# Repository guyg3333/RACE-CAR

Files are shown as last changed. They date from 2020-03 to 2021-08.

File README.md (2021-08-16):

# RACE-CAR

This repository contain my Academic engineering final project, which try to suggest a method of organizing information traffic in autonomous vehicles,

The problem I wanted to solve is how to expand the current communication method to support Advanced Drive assist application.

The proposed solution is to build a network built from a combination of CAN bus and Ethernet interfaces, were Ethernet used as backbone.

To bridge between the two interfaces I suggested to add dedicated module That I call  "Gateway Node",

The Gateway Node aim to manage the car data traffic and with him create a hierarchical Democratic multi master network were every node can exchange data.

### Network components
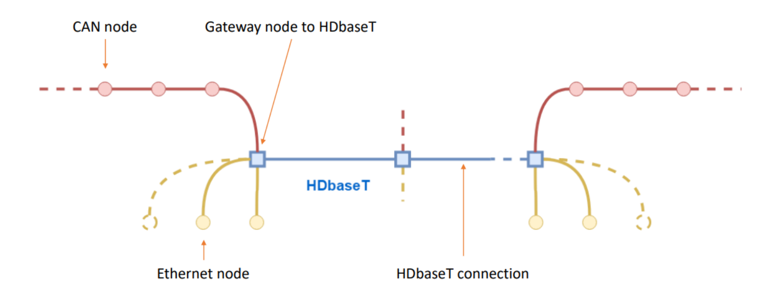
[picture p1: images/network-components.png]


### Network concept

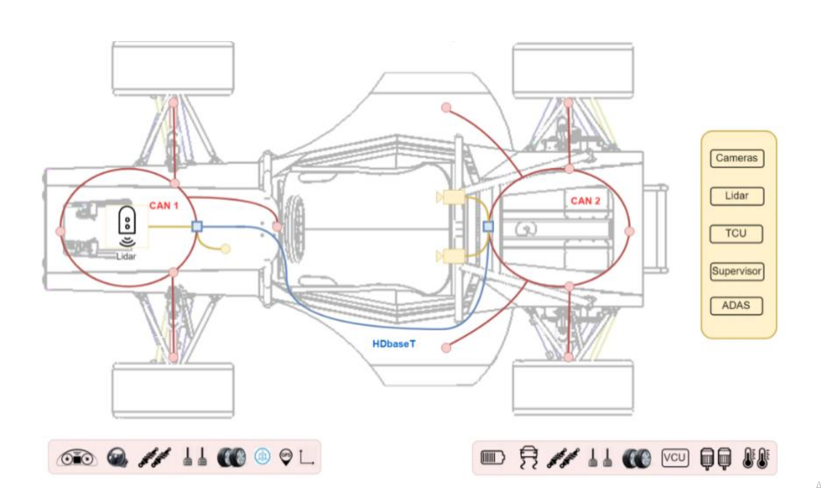
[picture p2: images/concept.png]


### Gateway Node 3D Model

I design and implement the network module "Gateway Node"

To meet the requirements of critical information passing through a vehicle, the Ethernet interface supports the AVB protocol to Ensure real time policy. [Link to PCB repository ](https://github.com/guyg3333/AVB_Ethernet_switch_with_CAN_bus)

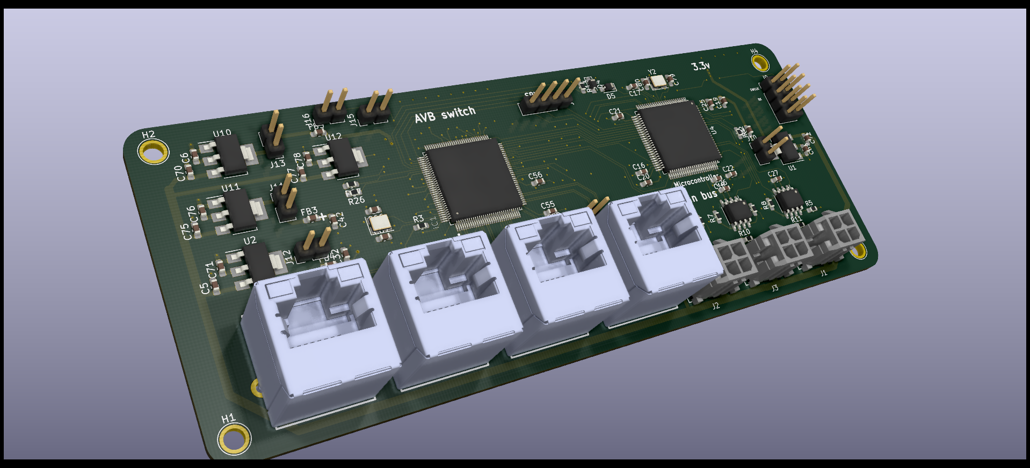
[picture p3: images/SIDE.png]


### CAN Node 3D Model

### Ben Gurion Racing

The component was assimilated in Ben-Gurion University FSAE electric car in 2019

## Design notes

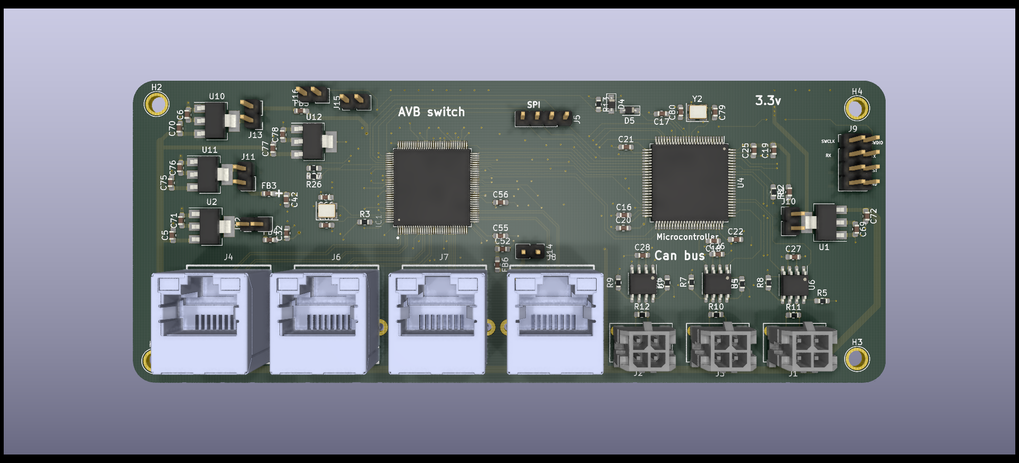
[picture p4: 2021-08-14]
images/TOP.png

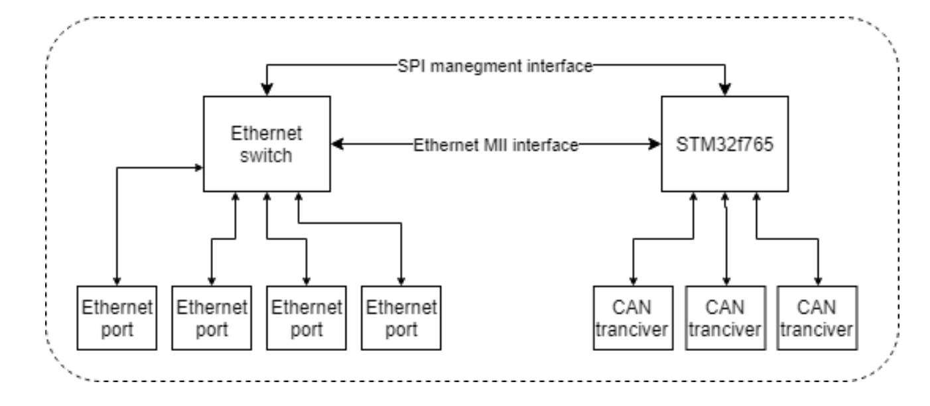
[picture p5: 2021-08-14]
images/block_diagram.png

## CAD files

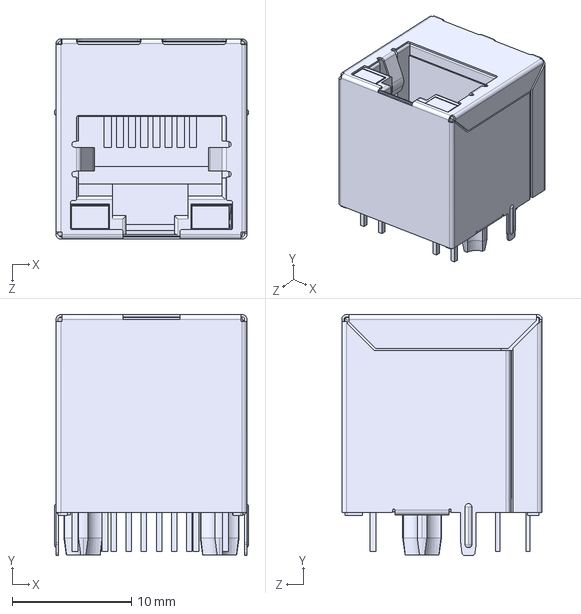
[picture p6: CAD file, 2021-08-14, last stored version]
AVB Ethernet switch with Can bus/3d/JD2_JXD2-0010N.STEP
16.3 x 20.2 x 16.8 mm

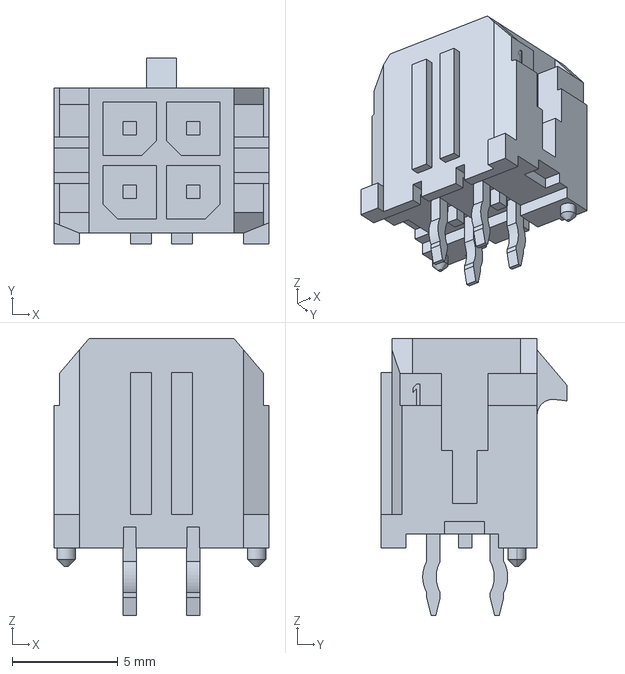
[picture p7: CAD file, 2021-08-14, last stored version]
AVB_Ethernet_switch_with_CAN_bus/3d/430450413.STEP
10.2 x 8.77 x 13.1 mm

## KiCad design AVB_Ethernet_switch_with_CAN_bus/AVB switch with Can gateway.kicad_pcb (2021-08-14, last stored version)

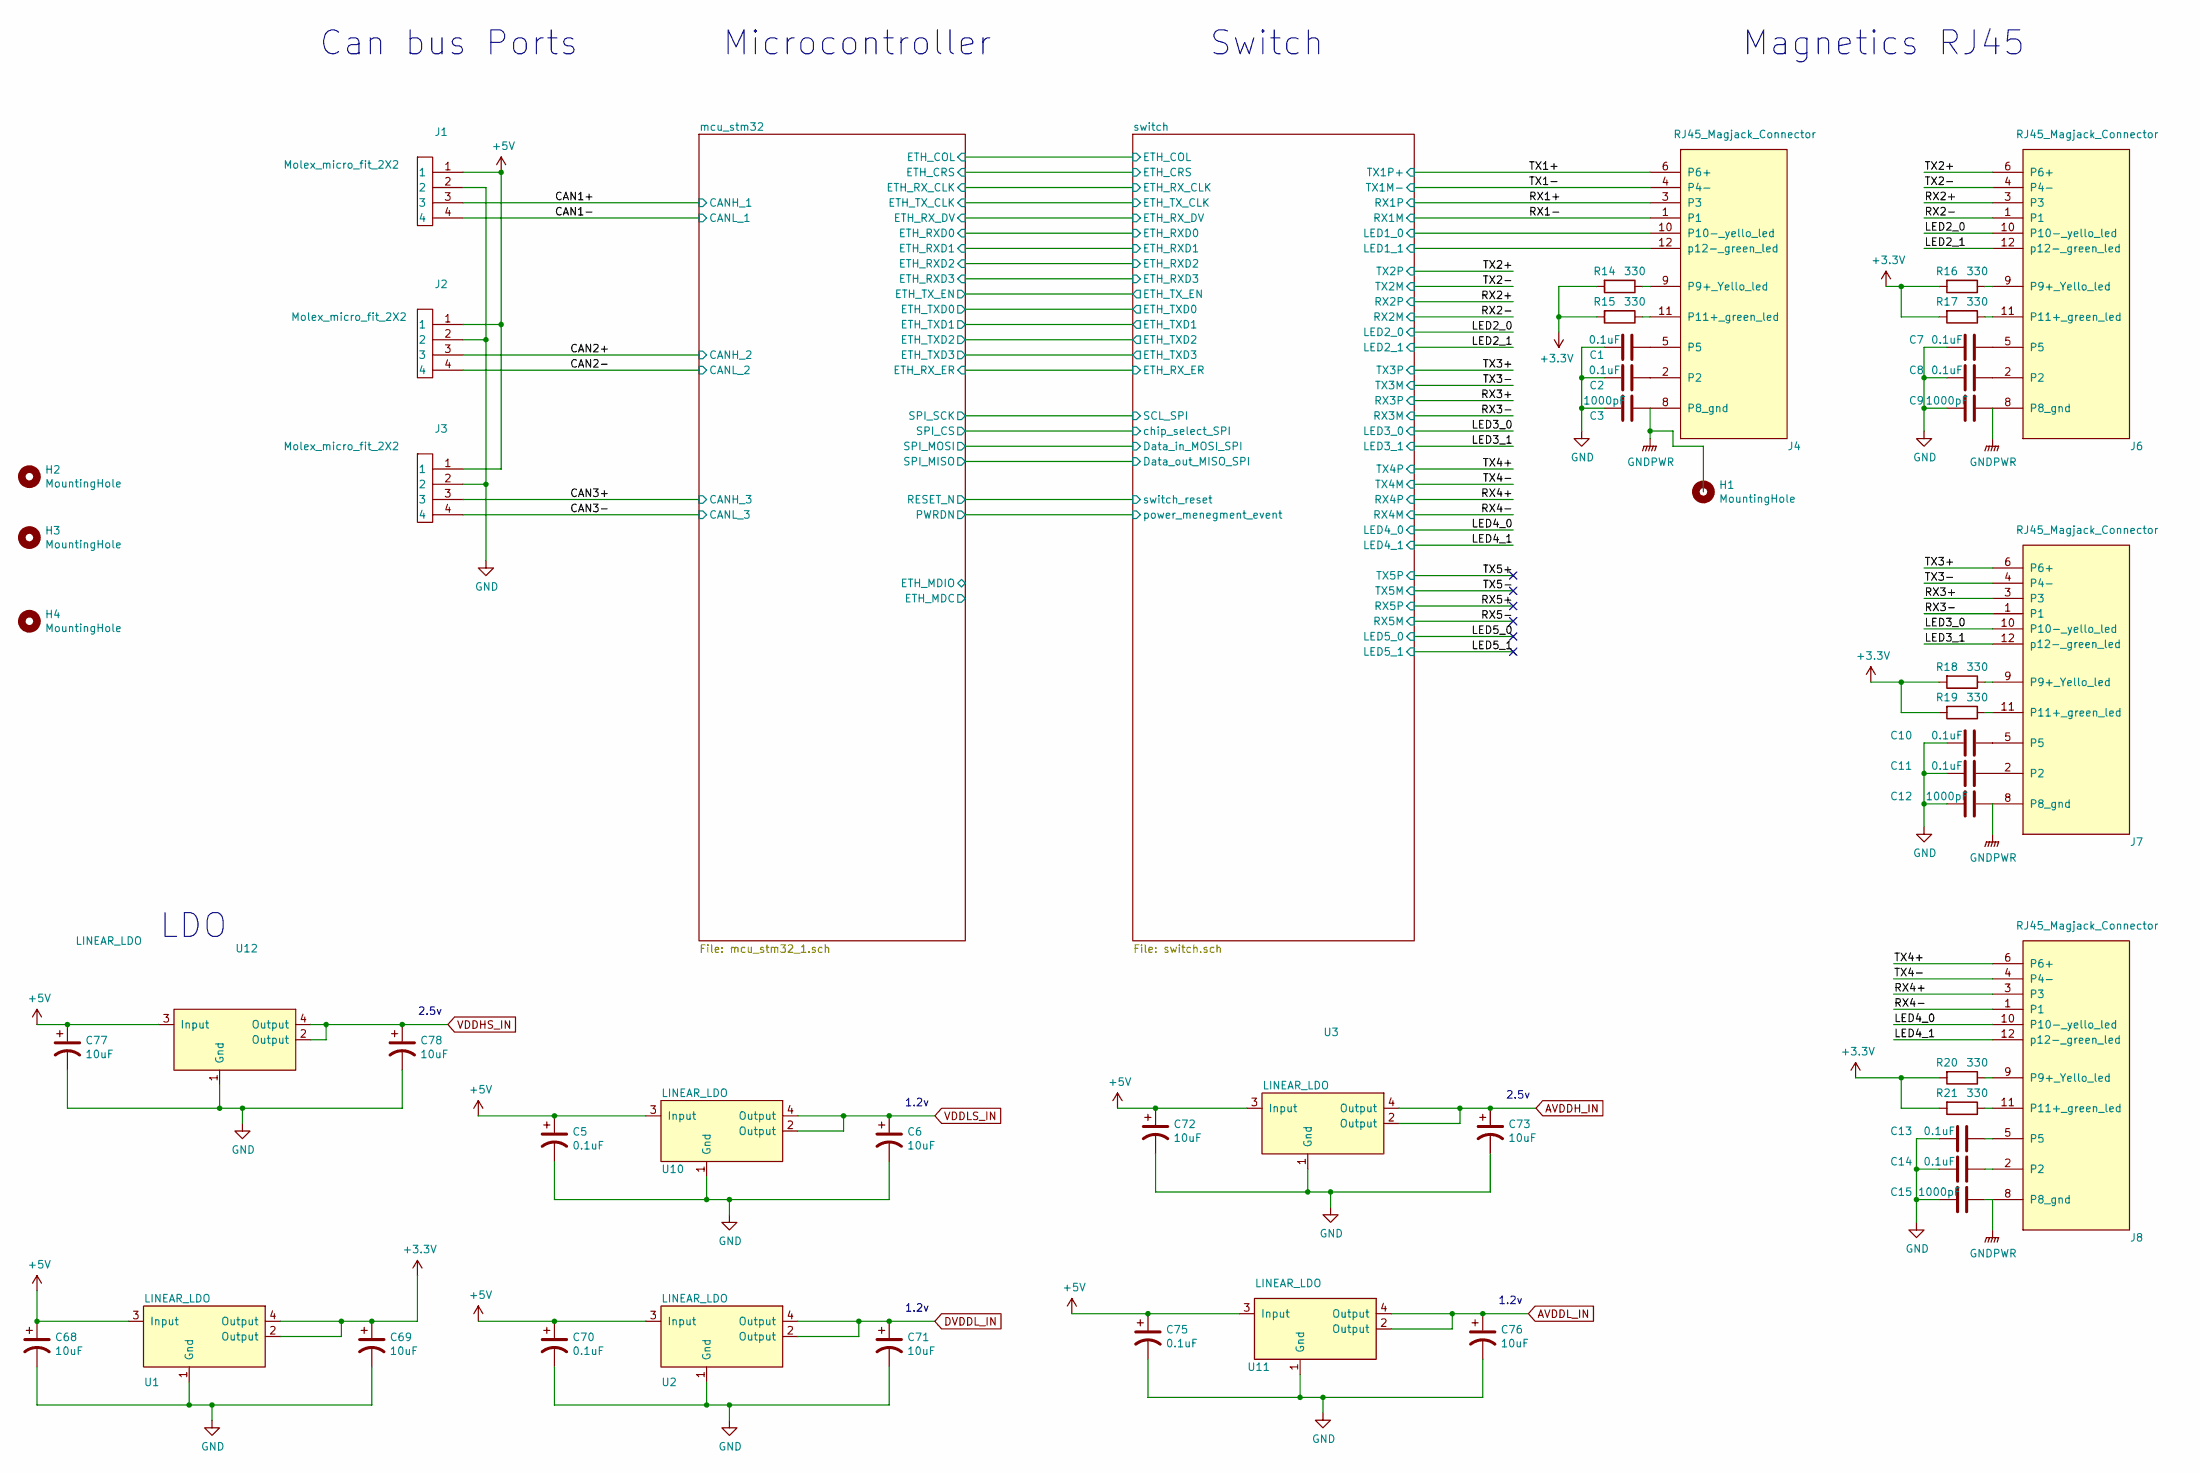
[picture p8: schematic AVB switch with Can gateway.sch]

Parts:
C1, C2, C7, C8, C10, C11, C13, C14: 0.1uF; C_0603_1608Metric_Pad1.05x0.95mm_HandSolder; Manufacturer_Part_Number C0603C104J4RACTU‎‏
C3, C9, C12, C15: 1000pF; C_0603_1608Metric_Pad1.05x0.95mm_HandSolder; Manufacturer_Part_Number C0603V102KDRAC7867‎‏
C5, C70, C75: 0.1uF; C_0603_1608Metric_Pad1.05x0.95mm_HandSolder; Manufacturer_Part_Number CC1206KRX7R9BB104‎‏
C6, C68, C69, C71, C72, C73, C76, C77, C78: 10uF; C_0603_1608Metric_Pad1.05x0.95mm_HandSolder; Manufacturer_Part_Number T520A106M010ATE080‎‏
H1, H2, H3, H4: MountingHole; 1pin
J1, J2, J3: Molex_micro_fit_2X2; Manufacturer_Part_Number ‏‎CONN HEADER VERT 4POS 3MM‎‏
J4, J6, J7, J8: RJ45_Magjack_Connector; RJ45_MAGJACK_1PORT_100_BASE-T‎‏; Manufacturer_Part_Number ‏‎JD2-0010NL‎‏
R14, R15, R16, R17, R18, R19, R20, R21: 330; R_0603_1608Metric_Pad1.05x0.95mm_HandSolder; Manufacturer_Part_Number ‏‎CR0603-JW-331ELF‎‏
U1: LINEAR_LDO; SOT-223; Manufacturer_Part_Number NCP1117ST33T3G‎‏
U2, U10, U11: LINEAR_LDO; SOT-223; Manufacturer_Part_Number LD1117AS12TR‎‏
U3, U12: LINEAR_LDO; SOT-223; Manufacturer_Part_Number ‏‎NCV1117ST25T3G‎‏

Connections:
+3V3: C69.1, R14.2, R15.2, R16.2, R17.2, R18.2, R19.2, R20.2, R21.2, U1.2 (Output), U1.4 (Output); also elsewhere on the board
+5V: C5.1, C68.1, C70.1, C72.1, C75.1, C77.1, J1.1, J2.1, J3.1, U1.3 (Input), U2.3 (Input), U3.3 (Input), U10.3 (Input), U11.3 (Input), U12.3 (Input)
/CAN1+: J1.3; also elsewhere on the board
/CAN1-: J1.4; also elsewhere on the board
/CAN2+: J2.3; also elsewhere on the board
/CAN2-: J2.4; also elsewhere on the board
/CAN3+: J3.3; also elsewhere on the board
/CAN3-: J3.4; also elsewhere on the board
/LED2_0: J6.10 (P10-_yello_led); also elsewhere on the board
/LED2_1: J6.12 (p12-_green_led); also elsewhere on the board
/LED3_0: J7.10 (P10-_yello_led); also elsewhere on the board
/LED3_1: J7.12 (p12-_green_led); also elsewhere on the board
/LED4_0: J8.10 (P10-_yello_led); also elsewhere on the board
/LED4_1: J8.12 (p12-_green_led); also elsewhere on the board
/RX1+: J4.3; also elsewhere on the board
/RX1-: J4.1; also elsewhere on the board
/RX2+: J6.3; also elsewhere on the board
/RX2-: J6.1; also elsewhere on the board
/RX3+: J7.3; also elsewhere on the board
/RX3-: J7.1; also elsewhere on the board
/RX4+: J8.3; also elsewhere on the board
/RX4-: J8.1; also elsewhere on the board
/TX1+: J4.6 (P6+); also elsewhere on the board
/TX1-: J4.4 (P4-); also elsewhere on the board
/TX2+: J6.6 (P6+); also elsewhere on the board
/TX2-: J6.4 (P4-); also elsewhere on the board
/TX3+: J7.6 (P6+); also elsewhere on the board
/TX3-: J7.4 (P4-); also elsewhere on the board
/TX4+: J8.6 (P6+); also elsewhere on the board
/TX4-: J8.4 (P4-); also elsewhere on the board
/switch/LED1_0: J4.10 (P10-_yello_led); also elsewhere on the board
/switch/LED1_1: J4.12 (p12-_green_led); also elsewhere on the board
AVDDH_IN: C73.1, U3.2 (Output), U3.4 (Output); also elsewhere on the board
AVDDL_IN: C76.1, U11.2 (Output), U11.4 (Output); also elsewhere on the board
DVDDL_IN: C71.1, U2.2 (Output), U2.4 (Output); also elsewhere on the board
GND: C1.2, C2.2, C3.2, C5.2, C6.2, C7.2, C8.2, C9.2, C10.2, C11.2, C12.2, C13.2, C14.2, C15.2, C68.2, C69.2, C70.2, C71.2, C72.2, C73.2, C75.2, C76.2, C77.2, C78.2, J1.2, J2.2, J3.2, U1.1 (Gnd), U2.1 (Gnd), U3.1 (Gnd), U10.1 (Gnd), U11.1 (Gnd), U12.1 (Gnd); also elsewhere on the board
GNDPWR: C3.1, C9.1, C12.1, C15.1, J4.8 (P8_gnd), J6.8 (P8_gnd), J7.8 (P8_gnd), J8.8 (P8_gnd)
unnamed: C1.1, J4.5
unnamed: C2.1, J4.2
unnamed: C7.1, J6.5
unnamed: C8.1, J6.2
unnamed: C10.1, J7.5
unnamed: C11.1, J7.2
unnamed: C13.1, J8.5
unnamed: C14.1, J8.2
unnamed: J4.9 (P9+_Yello_led), R14.1
unnamed: J4.11 (P11+_green_led), R15.1
unnamed: J6.9 (P9+_Yello_led), R16.1
unnamed: J6.11 (P11+_green_led), R17.1
unnamed: J7.9 (P9+_Yello_led), R18.1
unnamed: J7.11 (P11+_green_led), R19.1
unnamed: J8.9 (P9+_Yello_led), R20.1
unnamed: J8.11 (P11+_green_led), R21.1
VDDHS_IN: C78.1, U12.2 (Output), U12.4 (Output); also elsewhere on the board
VDDLS_IN: C6.1, U10.2 (Output), U10.4 (Output); also elsewhere on the board

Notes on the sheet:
Switch
Microcontroller
Can bus Ports
Magnetics RJ45
LDO
2.5v
1.2v

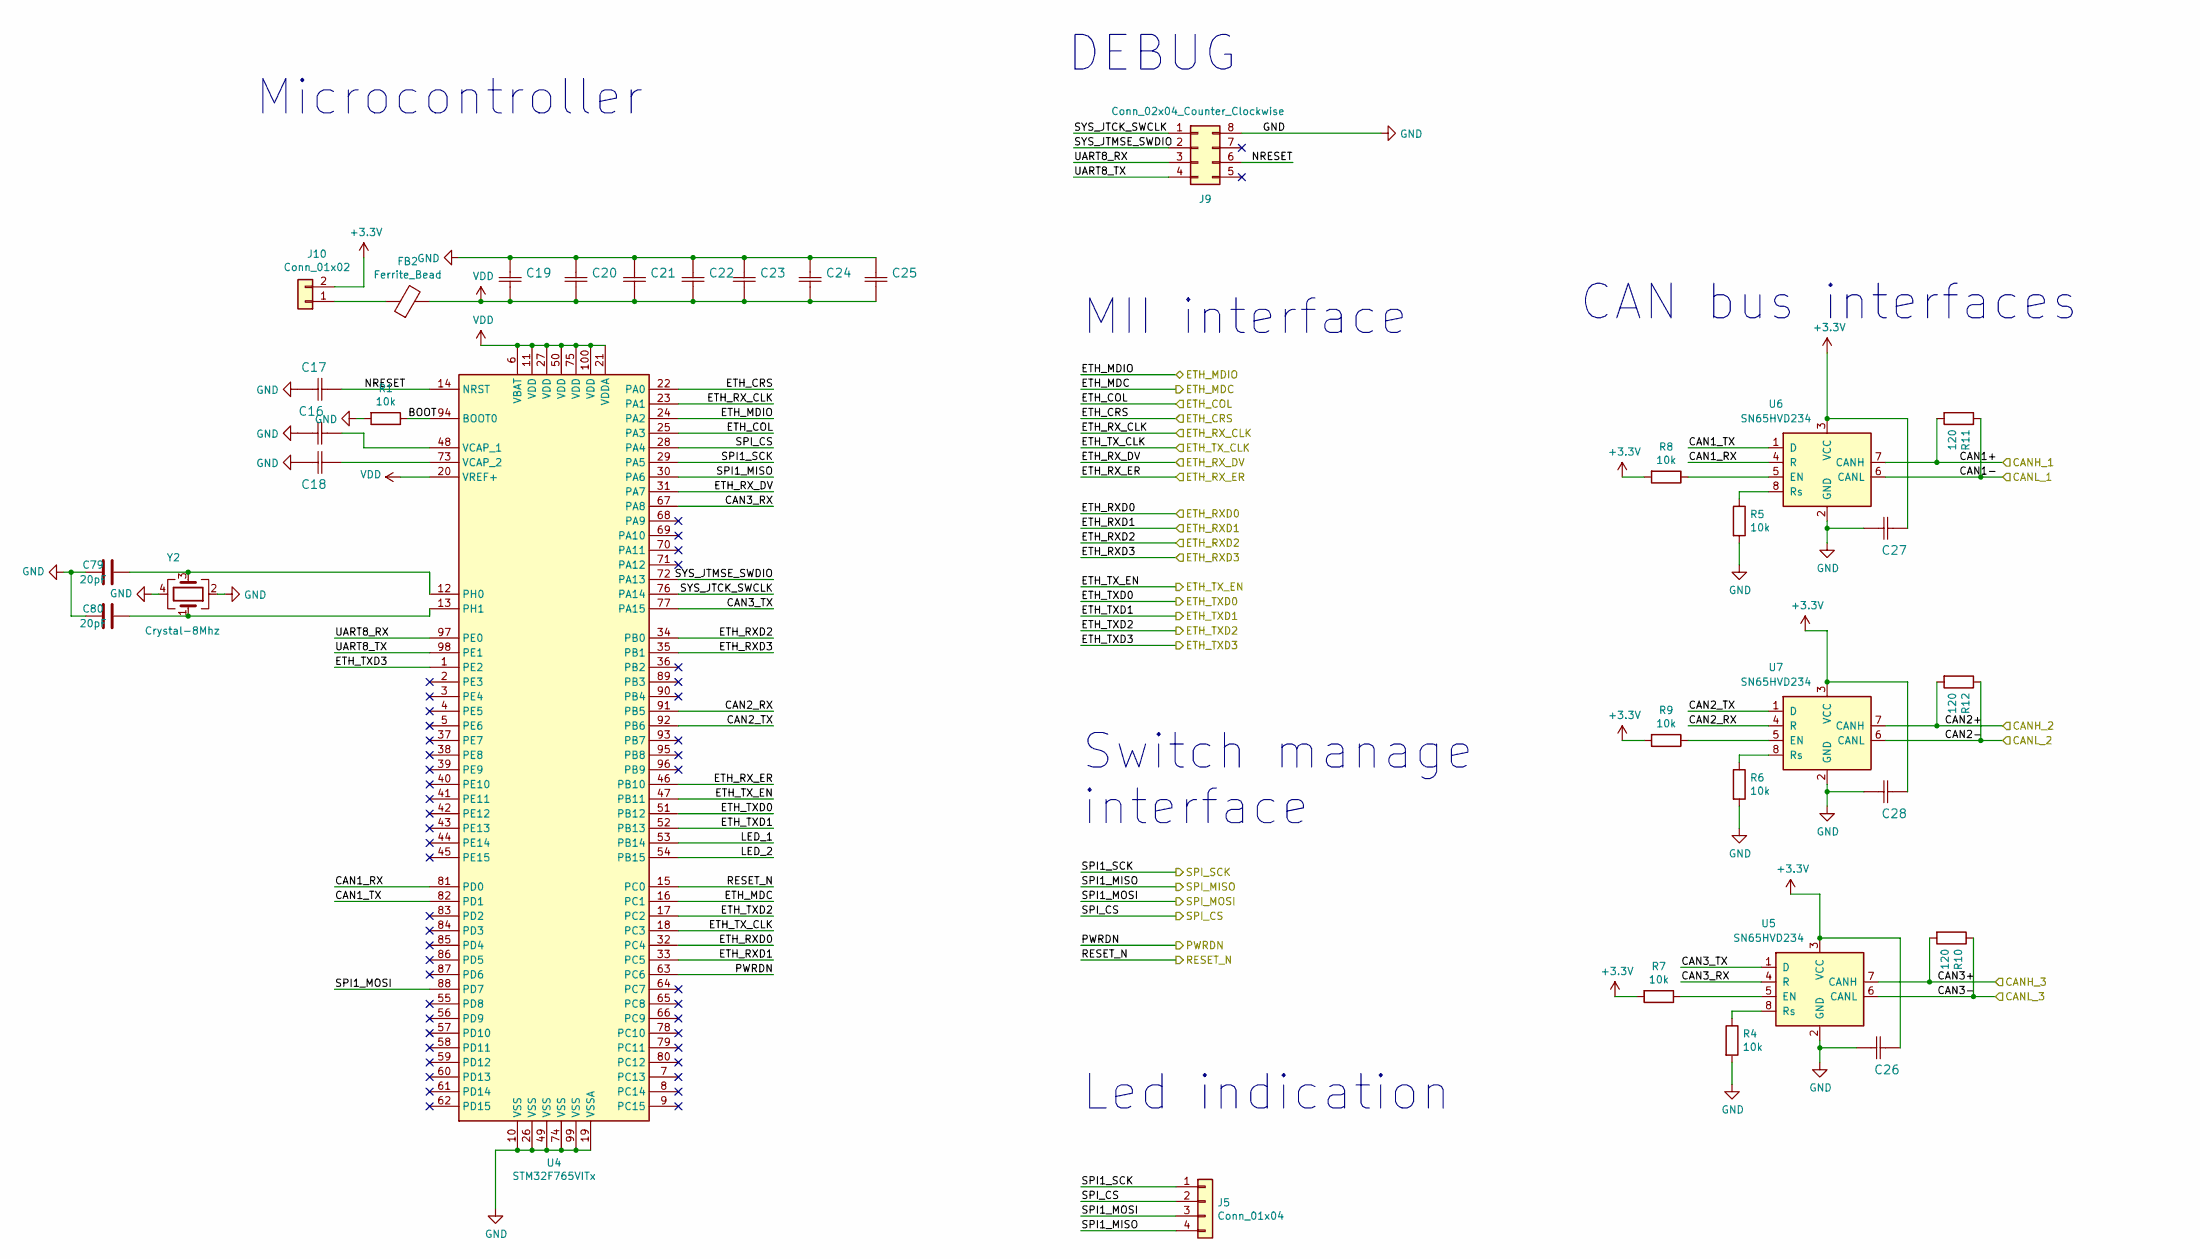
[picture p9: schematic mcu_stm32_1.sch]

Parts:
C16, C18, C26, C27, C28: 2.2uF; C_0603_1608Metric_Pad1.05x0.95mm_HandSolder; Manufacturer_Part_Number CL10A225KP8NNNC‎‏
C17, C20, C21, C22, C23, C24, C25: 0.1uF; C_0603_1608Metric_Pad1.05x0.95mm_HandSolder; Manufacturer_Part_Number C0603C104J4RACTU‎‏
C19: 4.7uF; C_0603_1608Metric_Pad1.05x0.95mm_HandSolder; Manufacturer_Part_Number CL10B475KQ8NQNC‎‏
C79, C80: 20pF; C_0603_1608Metric_Pad1.05x0.95mm_HandSolder; Manufacturer_Part_Number CL10C360JB8NNNC‎‏
FB2: Ferrite_Bead; C_0603_1608Metric_Pad1.05x0.95mm_HandSolder
J5: Conn_01x04; PinHeader_1x04_P2.54mm_Vertical
J9: Conn_02x04_Counter_Clockwise; PinHeader_2x04_P2.54mm_Vertical
J10: Conn_01x02; PinHeader_1x02_P2.54mm_Vertical
R1: 10k; R_0603_1608Metric_Pad1.05x0.95mm_HandSolder
R4, R5, R6, R7, R8, R9: 10k; R_0603_1608Metric_Pad1.05x0.95mm_HandSolder; Manufacturer_Part_Number RNCP0603FTD10K0‎‏
R10, R11, R12: 120; R_0603_1608Metric_Pad1.05x0.95mm_HandSolder; Manufacturer_Part_Number ‏‎CRGCQ0603F120R‎‏
U4: STM32F765VITx; LQFP-100_14x14mm_P0.5mm; Manufacturer_Part_Number ‏‎STM32F765VIT6‎‏
U5, U6, U7: SN65HVD234; SOIC-8_3.9x4.9mm_P1.27mm; Manufacturer_Part_Number SN65HVD234DR‎‏
Y2: Crystal-8Mhz; Crystal_SMD_3225-4Pin_3.2x2.5mm; Manufacturer_Part_Number ‏‎ECS-80-10-30B-CWN-TR‎‏

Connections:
+3V3: C26.1, C27.1, C28.1, J10.2, R7.2, R8.2, R9.2, U5.3 (VCC), U6.3 (VCC), U7.3 (VCC); also elsewhere on the board
/CAN1+: R11.2, U6.7 (CANH); also elsewhere on the board
/CAN1-: R11.1, U6.6 (CANL); also elsewhere on the board
/CAN2+: R12.2, U7.7 (CANH); also elsewhere on the board
/CAN2-: R12.1, U7.6 (CANL); also elsewhere on the board
/CAN3+: R10.2, U5.7 (CANH); also elsewhere on the board
/CAN3-: R10.1, U5.6 (CANL); also elsewhere on the board
/mcu_stm32/BOOT: R1.1, U4.94 (BOOT0)
/mcu_stm32/CAN1_RX: U4.81 (PD0), U6.4 (R)
/mcu_stm32/CAN1_TX: U4.82 (PD1), U6.1 (D)
/mcu_stm32/CAN2_RX: U4.91 (PB5), U7.4 (R)
/mcu_stm32/CAN2_TX: U4.92 (PB6), U7.1 (D)
/mcu_stm32/CAN3_RX: U4.67 (PA8), U5.4 (R)
/mcu_stm32/CAN3_TX: U4.77 (PA15), U5.1 (D)
/mcu_stm32/ETH_COL: U4.25 (PA3); also elsewhere on the board
/mcu_stm32/ETH_CRS: U4.22 (PA0); also elsewhere on the board
/mcu_stm32/ETH_MDC: U4.16 (PC1)
/mcu_stm32/ETH_MDIO: U4.24 (PA2)
/mcu_stm32/ETH_RXD0: U4.32 (PC4); also elsewhere on the board
/mcu_stm32/ETH_RXD1: U4.33 (PC5); also elsewhere on the board
/mcu_stm32/ETH_RXD2: U4.34 (PB0); also elsewhere on the board
/mcu_stm32/ETH_RXD3: U4.35 (PB1); also elsewhere on the board
/mcu_stm32/ETH_RX_CLK: U4.23 (PA1); also elsewhere on the board
/mcu_stm32/ETH_RX_DV: U4.31 (PA7); also elsewhere on the board
/mcu_stm32/ETH_RX_ER: U4.46 (PB10); also elsewhere on the board
/mcu_stm32/ETH_TXD0: U4.51 (PB12); also elsewhere on the board
/mcu_stm32/ETH_TXD1: U4.52 (PB13); also elsewhere on the board
/mcu_stm32/ETH_TXD2: U4.17 (PC2); also elsewhere on the board
/mcu_stm32/ETH_TXD3: U4.1 (PE2); also elsewhere on the board
/mcu_stm32/ETH_TX_CLK: U4.18 (PC3); also elsewhere on the board
/mcu_stm32/ETH_TX_EN: U4.47 (PB11); also elsewhere on the board
/mcu_stm32/LED_1: U4.53 (PB14)
/mcu_stm32/LED_2: U4.54 (PB15)
/mcu_stm32/NRESET: C17.1, J9.6, U4.14 (NRST)
/mcu_stm32/PWRDN: U4.63 (PC6)
/mcu_stm32/RESET_N: U4.15 (PC0); also elsewhere on the board
/mcu_stm32/SPI_CS: J5.2, U4.28 (PA4); also elsewhere on the board
/mcu_stm32/SYS_JTCK_SWCLK: J9.1, U4.76 (PA14)
/mcu_stm32/SYS_JTMSE_SWDIO: J9.2, U4.72 (PA13)
/mcu_stm32/UART8_RX: J9.3, U4.97 (PE0)
/mcu_stm32/UART8_TX: J9.4, U4.98 (PE1)
/switch/Data_in_MOSI_SPI: J5.3, U4.88 (PD7); also elsewhere on the board
/switch/Data_out_MISO_SPI: J5.4, U4.30 (PA6); also elsewhere on the board
/switch/SCL_SPI: J5.1, U4.29 (PA5); also elsewhere on the board
GND: C16.1, C17.2, C18.2, C19.1, C20.1, C21.1, C22.1, C23.1, C24.1, C25.1, C26.2, C27.2, C28.2, C79.2, C80.2, J9.8, R1.2, R4.2, R5.2, R6.2, U4.10 (VSS), U4.19 (VSSA), U4.26 (VSS), U4.49 (VSS), U4.74 (VSS), U4.99 (VSS), U5.2 (GND), U6.2 (GND), U7.2 (GND), Y2.2, Y2.4; also elsewhere on the board
unnamed: C16.2, U4.48 (VCAP_1)
unnamed: C18.1, U4.73 (VCAP_2)
unnamed: C79.1, U4.12 (PH0), Y2.3
unnamed: C80.1, U4.13 (PH1), Y2.1
unnamed: FB2.1, J10.1
unnamed: R4.1, U5.8 (Rs)
unnamed: R5.1, U6.8 (Rs)
unnamed: R6.1, U7.8 (Rs)
unnamed: R7.1, U5.5 (EN)
unnamed: R8.1, U6.5 (EN)
unnamed: R9.1, U7.5 (EN)
VDD: C19.2, C20.2, C21.2, C22.2, C23.2, C24.2, C25.2, FB2.2, U4.6 (VBAT), U4.11 (VDD), U4.20 (VREF+), U4.21 (VDDA), U4.27 (VDD), U4.50 (VDD), U4.75 (VDD), U4.100 (VDD)

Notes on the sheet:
DEBUG
MII interface
CAN bus interfaces
Microcontroller
Switch manage interface
Led indication

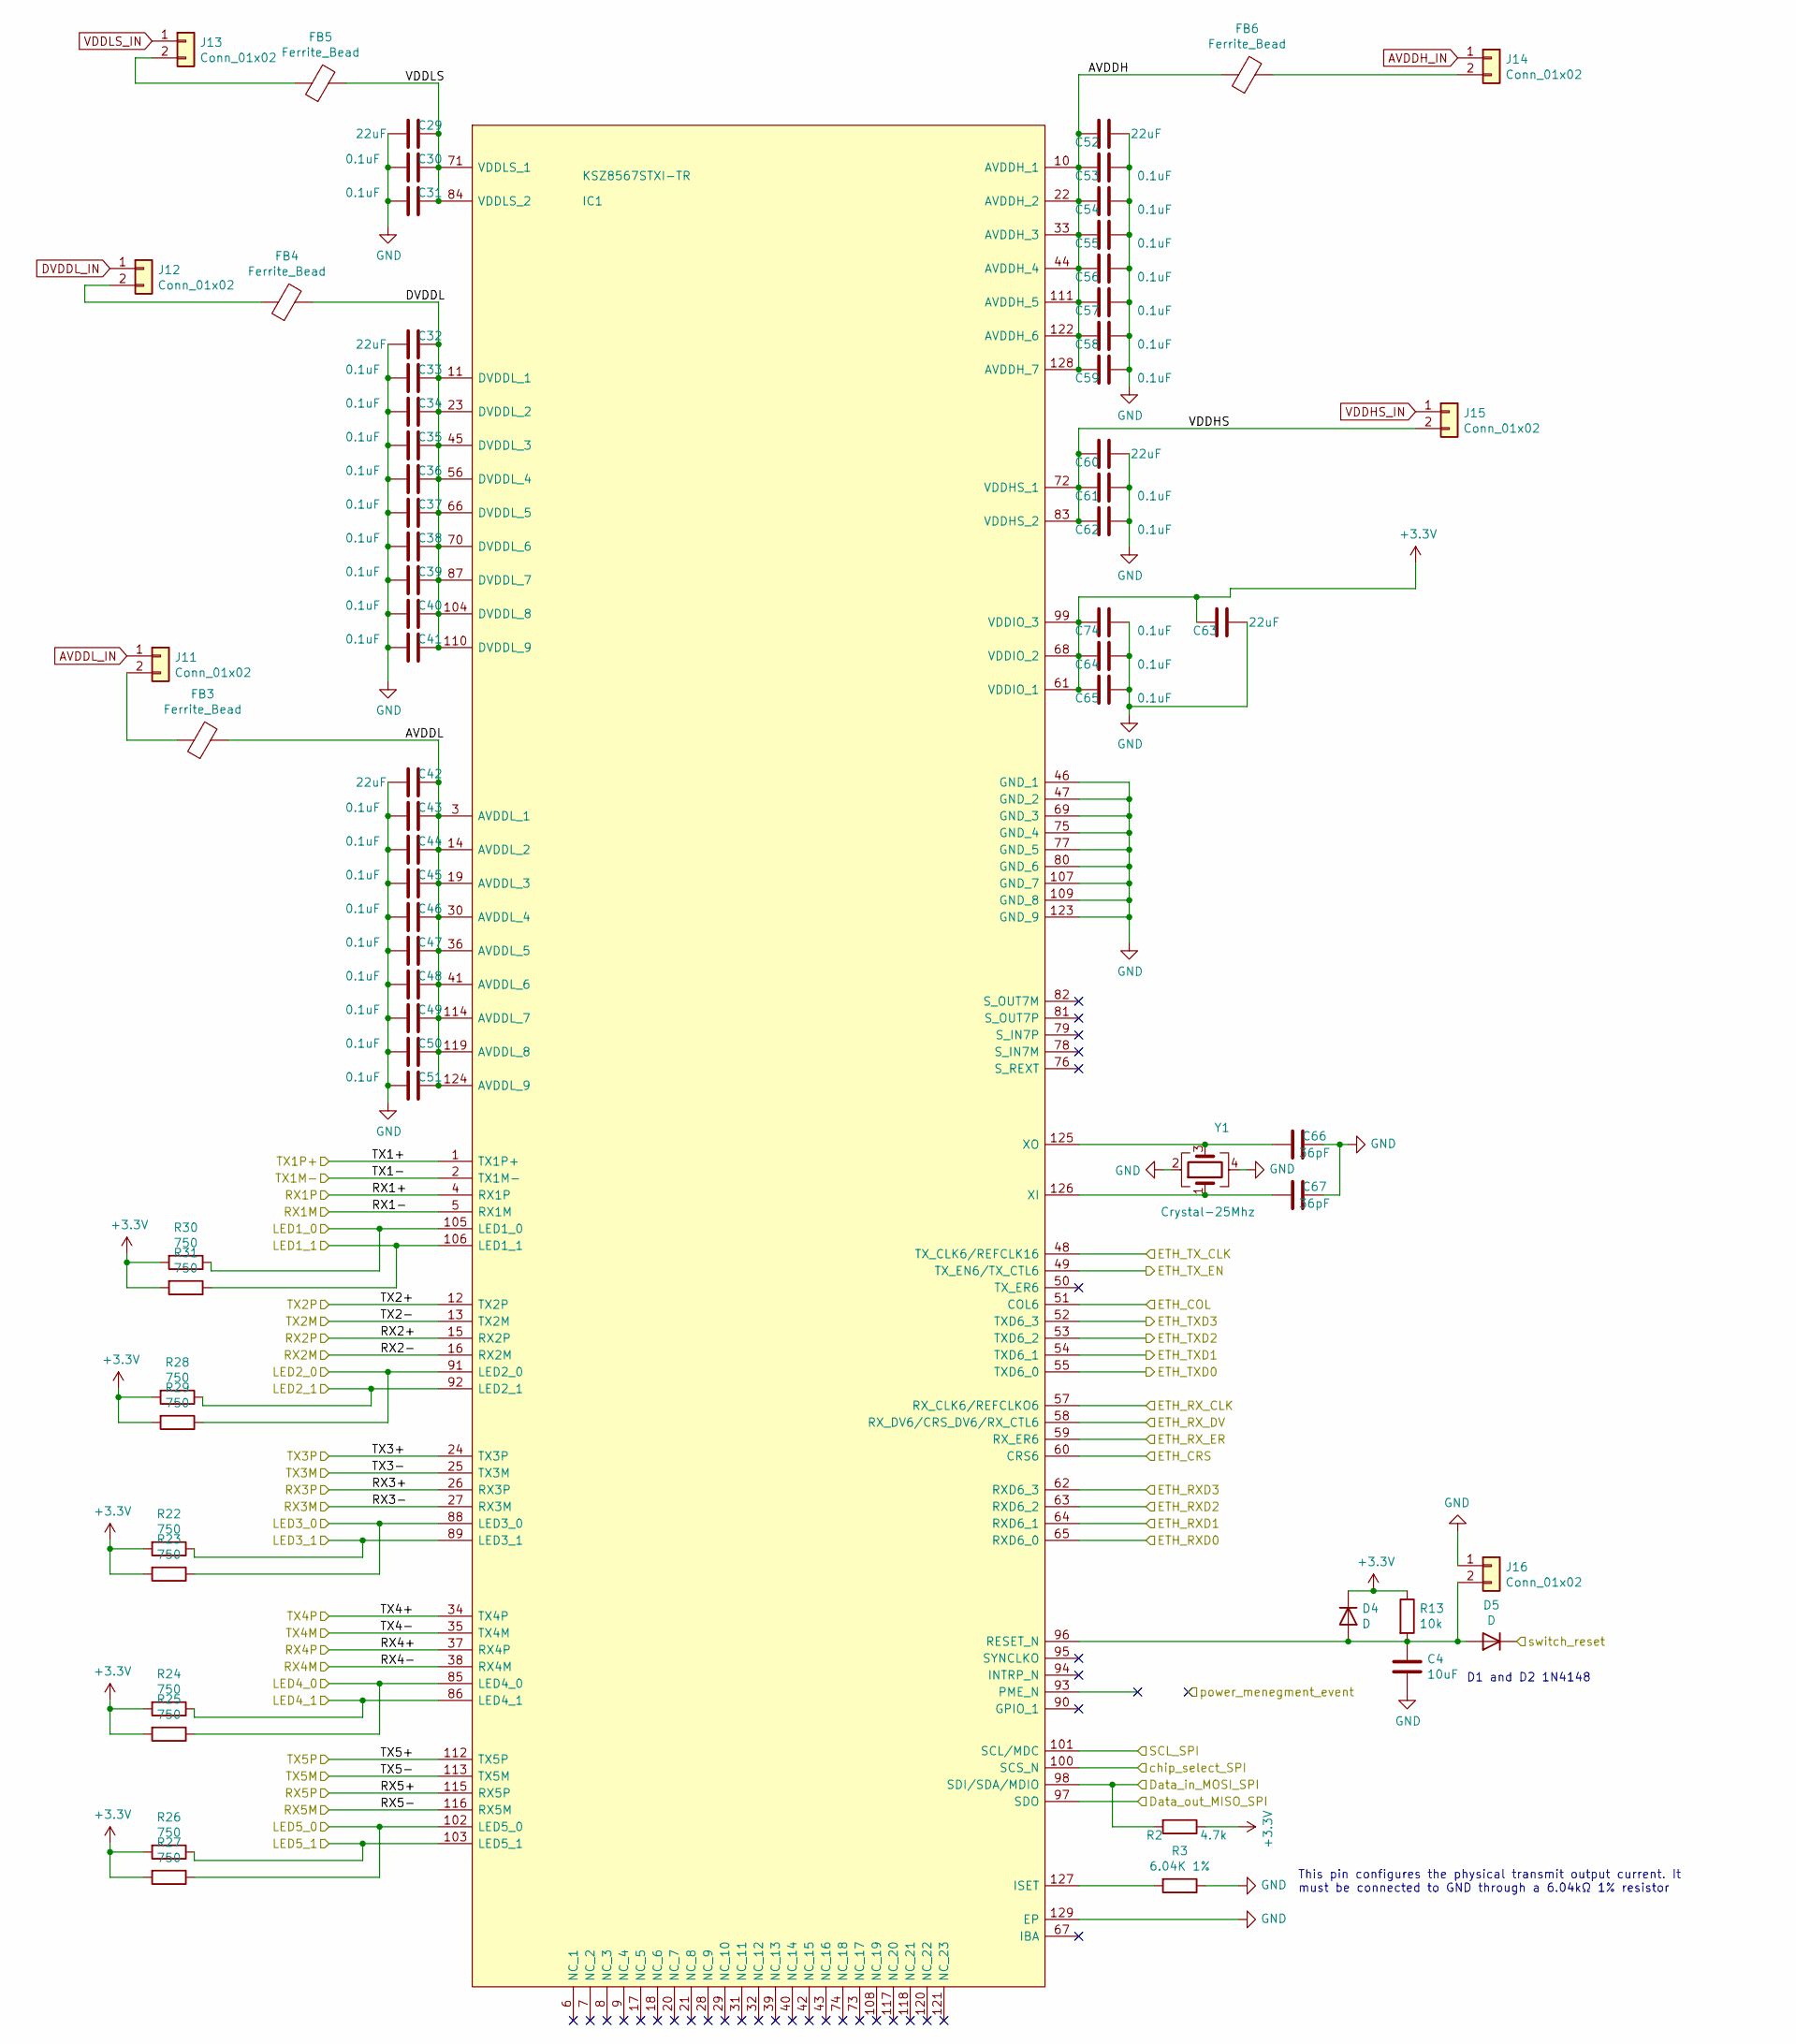
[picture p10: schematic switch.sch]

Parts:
C4: 10uF; C_0603_1608Metric_Pad1.05x0.95mm_HandSolder; Manufacturer_Part_Number CL10A106MQ8NNNC‎‏
C29, C32, C42, C52, C60, C63: 22uF; C_0603_1608Metric_Pad1.05x0.95mm_HandSolder; Manufacturer_Part_Number C1608X5R0J226M080AC‎‏
C30, C31, C33, C34, C35, C36, C37, C38, C39, C40, C41, C43, C44, C45, C46, C47, C48, C49, C50, C51, C53, C54, C55, C56, C57, C58, C59, C61, C62, C64, C65, C74: 0.1uF; C_0603_1608Metric_Pad1.05x0.95mm_HandSolder; Manufacturer_Part_Number C0603C104J4RACTU‎‏
C66, C67: 36pF; C_0603_1608Metric_Pad1.05x0.95mm_HandSolder; Manufacturer_Part_Number CL10C360JB8NNNC‎‏
D4, D5: D; D_SOD-323_HandSoldering; Manufacturer_Part_Number 1N4148WXTPMSCT
FB3, FB4, FB5, FB6: Ferrite_Bead; C_0603_1608Metric_Pad1.05x0.95mm_HandSolder
IC1: KSZ8567STXI-TR; QFP40P1600X1600X120-129N; Mouser Part Number 579-KSZ8567STXI-TR
J11, J12, J13, J14, J15, J16: Conn_01x02; PinHeader_1x02_P2.54mm_Vertical
R2: 4.7k; R_0603_1608Metric_Pad1.05x0.95mm_HandSolder; Manufacturer_Part_Number ‏‎RC0603JR-074K7L‎‏
R3: 6.04K 1%; R_0603_1608Metric_Pad1.05x0.95mm_HandSolder; Manufacturer_Part_Number RMCF0603FT6K04‎‏
R13: 10k; R_0603_1608Metric_Pad1.05x0.95mm_HandSolder; Manufacturer_Part_Number RNCP0603FTD10K0‎‏
R22, R23, R24, R25, R26, R27, R28, R29, R30, R31: 750; R_0603_1608Metric_Pad1.05x0.95mm_HandSolder
Y1: Crystal-25Mhz; Crystal_SMD_3225-4Pin_3.2x2.5mm; Manufacturer_Part_Number ‏‎FA-238 25.0000MB-C3‎‏

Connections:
+3V3: C63.1, C64.1, C65.1, C74.1, D4.1 (K), IC1.61 (VDDIO_1), IC1.68 (VDDIO_2), IC1.99 (VDDIO_3), R2.1, R13.1, R22.2, R23.2, R24.2, R25.2, R26.2, R27.2, R28.2, R29.2, R30.2, R31.2; also elsewhere on the board
/LED2_0: IC1.91 (LED2_0), R29.1; also elsewhere on the board
/LED2_1: IC1.92 (LED2_1), R28.1; also elsewhere on the board
/LED3_0: IC1.88 (LED3_0), R23.1; also elsewhere on the board
/LED3_1: IC1.89 (LED3_1), R22.1; also elsewhere on the board
/LED4_0: IC1.85 (LED4_0), R25.1; also elsewhere on the board
/LED4_1: IC1.86 (LED4_1), R24.1; also elsewhere on the board
/LED5_0: IC1.102 (LED5_0), R27.1
/LED5_1: IC1.103 (LED5_1), R26.1
/RX1+: IC1.4 (RX1P); also elsewhere on the board
/RX1-: IC1.5 (RX1M); also elsewhere on the board
/RX2+: IC1.15 (RX2P); also elsewhere on the board
/RX2-: IC1.16 (RX2M); also elsewhere on the board
/RX3+: IC1.26 (RX3P); also elsewhere on the board
/RX3-: IC1.27 (RX3M); also elsewhere on the board
/RX4+: IC1.37 (RX4P); also elsewhere on the board
/RX4-: IC1.38 (RX4M); also elsewhere on the board
/RX5+: IC1.115 (RX5P)
/RX5-: IC1.116 (RX5M)
/TX1+: IC1.1 (TX1P+); also elsewhere on the board
/TX1-: IC1.2 (TX1M-); also elsewhere on the board
/TX2+: IC1.12 (TX2P); also elsewhere on the board
/TX2-: IC1.13 (TX2M); also elsewhere on the board
/TX3+: IC1.24 (TX3P); also elsewhere on the board
/TX3-: IC1.25 (TX3M); also elsewhere on the board
/TX4+: IC1.34 (TX4P); also elsewhere on the board
/TX4-: IC1.35 (TX4M); also elsewhere on the board
/TX5+: IC1.112 (TX5P)
/TX5-: IC1.113 (TX5M)
/mcu_stm32/ETH_COL: IC1.51 (COL6); also elsewhere on the board
/mcu_stm32/ETH_CRS: IC1.60 (CRS6); also elsewhere on the board
/mcu_stm32/ETH_RXD0: IC1.65 (RXD6_0); also elsewhere on the board
/mcu_stm32/ETH_RXD1: IC1.64 (RXD6_1); also elsewhere on the board
/mcu_stm32/ETH_RXD2: IC1.63 (RXD6_2); also elsewhere on the board
/mcu_stm32/ETH_RXD3: IC1.62 (RXD6_3); also elsewhere on the board
/mcu_stm32/ETH_RX_CLK: IC1.57 (RX_CLK6/REFCLKO6); also elsewhere on the board
/mcu_stm32/ETH_RX_DV: IC1.58 (RX_DV6/CRS_DV6/RX_CTL6); also elsewhere on the board
/mcu_stm32/ETH_RX_ER: IC1.59 (RX_ER6); also elsewhere on the board
/mcu_stm32/ETH_TXD0: IC1.55 (TXD6_0); also elsewhere on the board
/mcu_stm32/ETH_TXD1: IC1.54 (TXD6_1); also elsewhere on the board
/mcu_stm32/ETH_TXD2: IC1.53 (TXD6_2); also elsewhere on the board
/mcu_stm32/ETH_TXD3: IC1.52 (TXD6_3); also elsewhere on the board
/mcu_stm32/ETH_TX_CLK: IC1.48 (TX_CLK6/REFCLK16); also elsewhere on the board
/mcu_stm32/ETH_TX_EN: IC1.49 (TX_EN6/TX_CTL6); also elsewhere on the board
/mcu_stm32/RESET_N: D5.1 (K); also elsewhere on the board
/mcu_stm32/SPI_CS: IC1.100 (SCS_N); also elsewhere on the board
/switch/AVDDH: C52.1, C53.1, C54.1, C55.1, C56.1, C57.1, C58.1, C59.1, FB6.1, IC1.10 (AVDDH_1), IC1.22 (AVDDH_2), IC1.33 (AVDDH_3), IC1.44 (AVDDH_4), IC1.111 (AVDDH_5), IC1.122 (AVDDH_6), IC1.128 (AVDDH_7)
/switch/AVDDL: C42.1, C43.1, C44.1, C45.1, C46.1, C47.1, C48.1, C49.1, C50.1, C51.1, FB3.2, IC1.3 (AVDDL_1), IC1.14 (AVDDL_2), IC1.19 (AVDDL_3), IC1.30 (AVDDL_4), IC1.36 (AVDDL_5), IC1.41 (AVDDL_6), IC1.114 (AVDDL_7), IC1.119 (AVDDL_8), IC1.124 (AVDDL_9)
/switch/DVDDL: C32.1, C33.1, C34.1, C35.1, C36.1, C37.1, C38.1, C39.1, C40.1, C41.1, FB4.2, IC1.11 (DVDDL_1), IC1.23 (DVDDL_2), IC1.45 (DVDDL_3), IC1.56 (DVDDL_4), IC1.66 (DVDDL_5), IC1.70 (DVDDL_6), IC1.87 (DVDDL_7), IC1.104 (DVDDL_8), IC1.110 (DVDDL_9)
/switch/Data_in_MOSI_SPI: IC1.98 (SDI/SDA/MDIO), R2.2; also elsewhere on the board
/switch/Data_out_MISO_SPI: IC1.97 (SDO); also elsewhere on the board
/switch/LED1_0: IC1.105 (LED1_0), R30.1; also elsewhere on the board
/switch/LED1_1: IC1.106 (LED1_1), R31.1; also elsewhere on the board
/switch/SCL_SPI: IC1.101 (SCL/MDC); also elsewhere on the board
/switch/VDDHS: C60.1, C61.1, C62.1, IC1.72 (VDDHS_1), IC1.83 (VDDHS_2), J15.2
/switch/VDDLS: C29.1, C30.1, C31.1, FB5.2, IC1.71 (VDDLS_1), IC1.84 (VDDLS_2)
AVDDH_IN: J14.1; also elsewhere on the board
AVDDL_IN: J11.1; also elsewhere on the board
DVDDL_IN: J12.1; also elsewhere on the board
GND: C4.2, C29.2, C30.2, C31.2, C32.2, C33.2, C34.2, C35.2, C36.2, C37.2, C38.2, C39.2, C40.2, C41.2, C42.2, C43.2, C44.2, C45.2, C46.2, C47.2, C48.2, C49.2, C50.2, C51.2, C52.2, C53.2, C54.2, C55.2, C56.2, C57.2, C58.2, C59.2, C60.2, C61.2, C62.2, C63.2, C64.2, C65.2, C66.2, C67.2, C74.2, IC1.46 (GND_1), IC1.47 (GND_2), IC1.69 (GND_3), IC1.75 (GND_4), IC1.77 (GND_5), IC1.80 (GND_6), IC1.107 (GND_7), IC1.109 (GND_8), IC1.123 (GND_9), IC1.129 (EP), J16.1, R3.1, Y1.2, Y1.4; also elsewhere on the board
unnamed: C4.1, D4.2 (A), D5.2 (A), IC1.96 (RESET_N), J16.2, R13.2
unnamed: C66.1, IC1.125 (XO), Y1.3
unnamed: C67.1, IC1.126 (XI), Y1.1
unnamed: FB3.1, J11.2
unnamed: FB4.1, J12.2
unnamed: FB5.1, J13.2
unnamed: FB6.2, J14.2
unnamed: IC1.127 (ISET), R3.2
VDDHS_IN: J15.1; also elsewhere on the board
VDDLS_IN: J13.1; also elsewhere on the board

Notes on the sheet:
This pin configures the physical transmit output current. It must be connected to GND through a 6.04kΩ 1% resistor
D1 and D2 1N4148

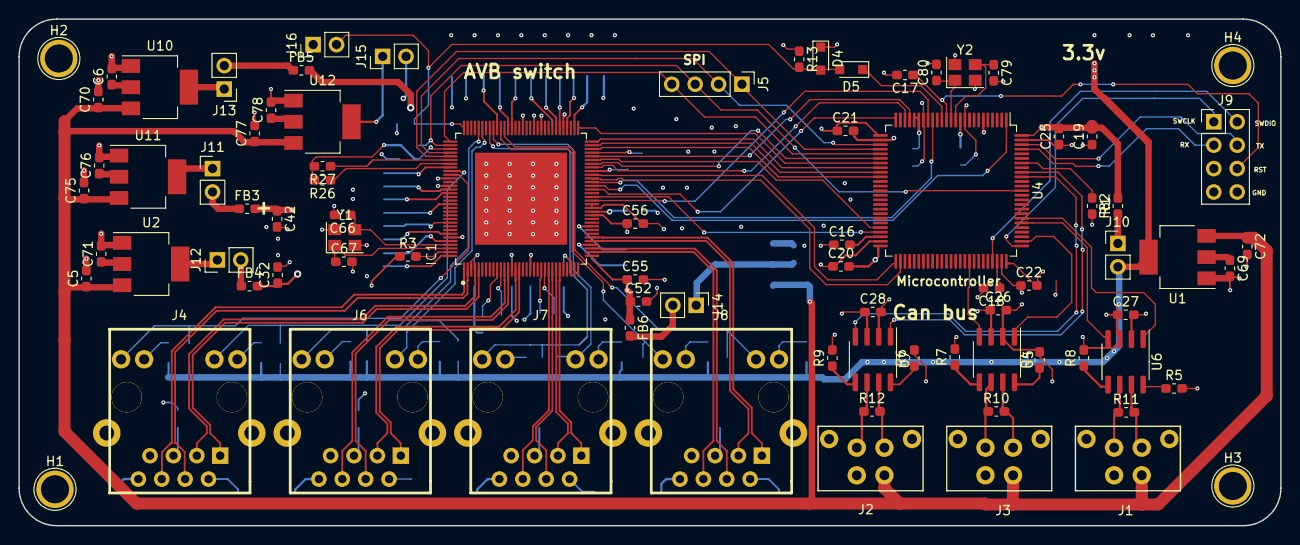
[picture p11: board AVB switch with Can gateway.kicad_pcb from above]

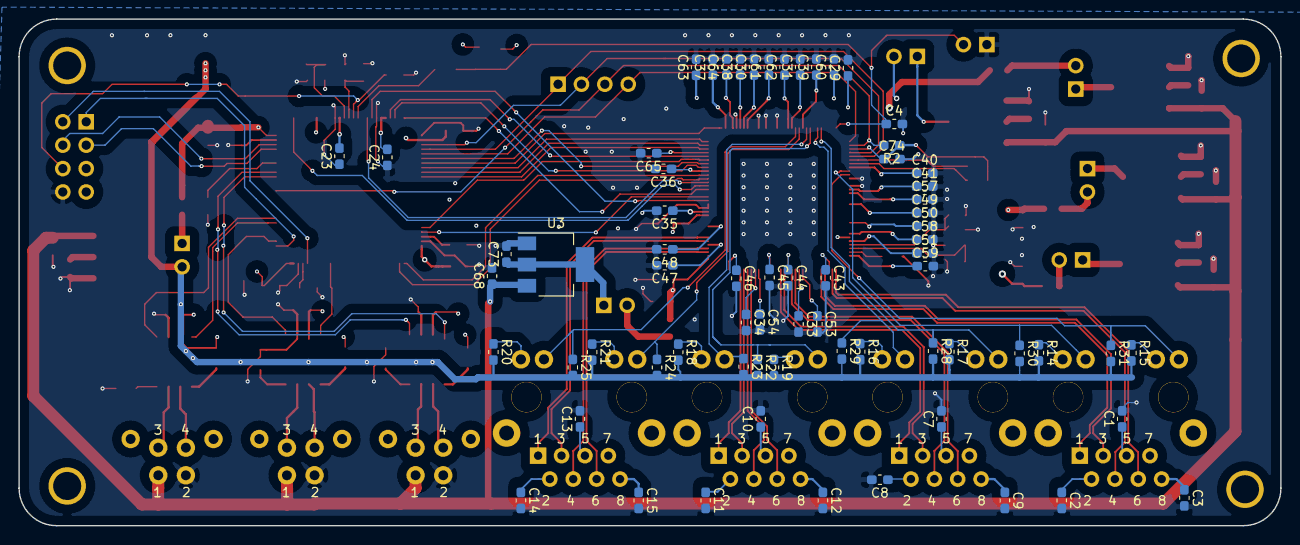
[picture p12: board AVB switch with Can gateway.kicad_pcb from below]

Board: 4 copper layers, 137.0 x 55.0 mm, 151 parts (68 on the bottom side), 114 nets.

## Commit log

2020-03-14 add pcb schematic of gateway
    aa
    [AVB switch with Can gateway-B.Cu.gbr, AVB switch with Can gateway-B.Mask.gbr, AVB switch with Can gateway-B.Paste.gbr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]
2021-08-14 change libery
    [430450413.STEP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]
2021-08-14 set README file
    [430450413.STEP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]
2021-08-14 move avb_pcb to another project
    [430450413.STEP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]
